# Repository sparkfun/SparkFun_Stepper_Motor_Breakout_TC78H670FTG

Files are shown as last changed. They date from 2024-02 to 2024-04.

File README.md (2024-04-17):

SparkFun Mini Stepper Motor Driver - TC78H670FTG
========================================

SparkFun Mini Stepper Motor Driver - TC78H670FTG

[*SparkFun Mini Stepper Motor Driver - TC78H670FTG (ROB-25167)*](https://sparkle.sparkfun.com/sparkle/products/25167)

The SparkFun Mini Stepper Motor Driver makes it easy to start developing with the TC78H670FTG bipolar stepper motor driver from Toshiba! With its compact size *(0.6" × 0.8")* and 0.1" pin spacing, the Mini Stepper Motor Driver is perfect for small projects or prototyping on breadboards. Use our extensive [Arduino Library](https://github.com/sparkfun/SparkFun_ProDriver_TC78H670FTG_Arduino_Library) with 10 examples, and you can quickly explore the many features of this precise and small package size motor driver IC.

With a high resolution motor control, down to 1/128th of a step, the Mini Stepper Motor Driver can be operated through traditional clock-in stepping or serial commands. Both methods are demonstrated in our Arduino Library. The serial command method is especially unique in that it allows the user to precisely control the phase, torque, current limit and mixed decay ratio of each coil immediately during stepping. Most stepper motor driver ICs require the use of an external trimpot to set the current limit, but with the Mini Stepper Motor Driver, you can precisely adjust it in software, via serial commands!

Repository Contents
-------------------

* **/Documentation** - Datasheets, additional product information
* **/Hardware** - Eagle design files (.brd, .sch)
* **/Hardware/Production** - Production panel files and gerbers (.brd)

Documentation
--------------

* **[Hookup Guide](https://learn.sparkfun.com/tutorials/1200)** - A hookup guide for the SparkFun ProDriver and Mini Stepper Motor Driver (TC78H670FTG)
* **[Arduino Library](https://github.com/sparkfun/SparkFun_ProDriver_TC78H670FTG_Arduino_Library)** - Basic Arduino Library for the SparkFun ProDriver and Mini Stepper Motor Driver (TC78H670FTG)

Product Variants
----------------
* SparkFun Mini Stepper Motor Driver - TC78H670FTG
  * [ROB-25167](https://www.sparkfun.com/products/25167)- v1.0, Initial Release
* SparkFun ProDriver - Stepper Motor Driver (TC78H670FTG)
  * [ROB-16836](https://www.sparkfun.com/products/16836)- v1.0, Initial Release

Product Versions
----------------
* [v01](https://github.com/sparkfun/SparkFun_Stepper_Motor_Breakout_TC78H670FTG/releases/tag/v10) - Initial Release

License Information
-------------------

This product is _**open source**_!

Please review the LICENSE.md file for license information.

If you have any questions or concerns on licensing, please contact technical support on our [SparkFun forums](https://forum.sparkfun.com/viewforum.php?f=152).

Distributed as-is; no warranty is given.

- Your friends at SparkFun.

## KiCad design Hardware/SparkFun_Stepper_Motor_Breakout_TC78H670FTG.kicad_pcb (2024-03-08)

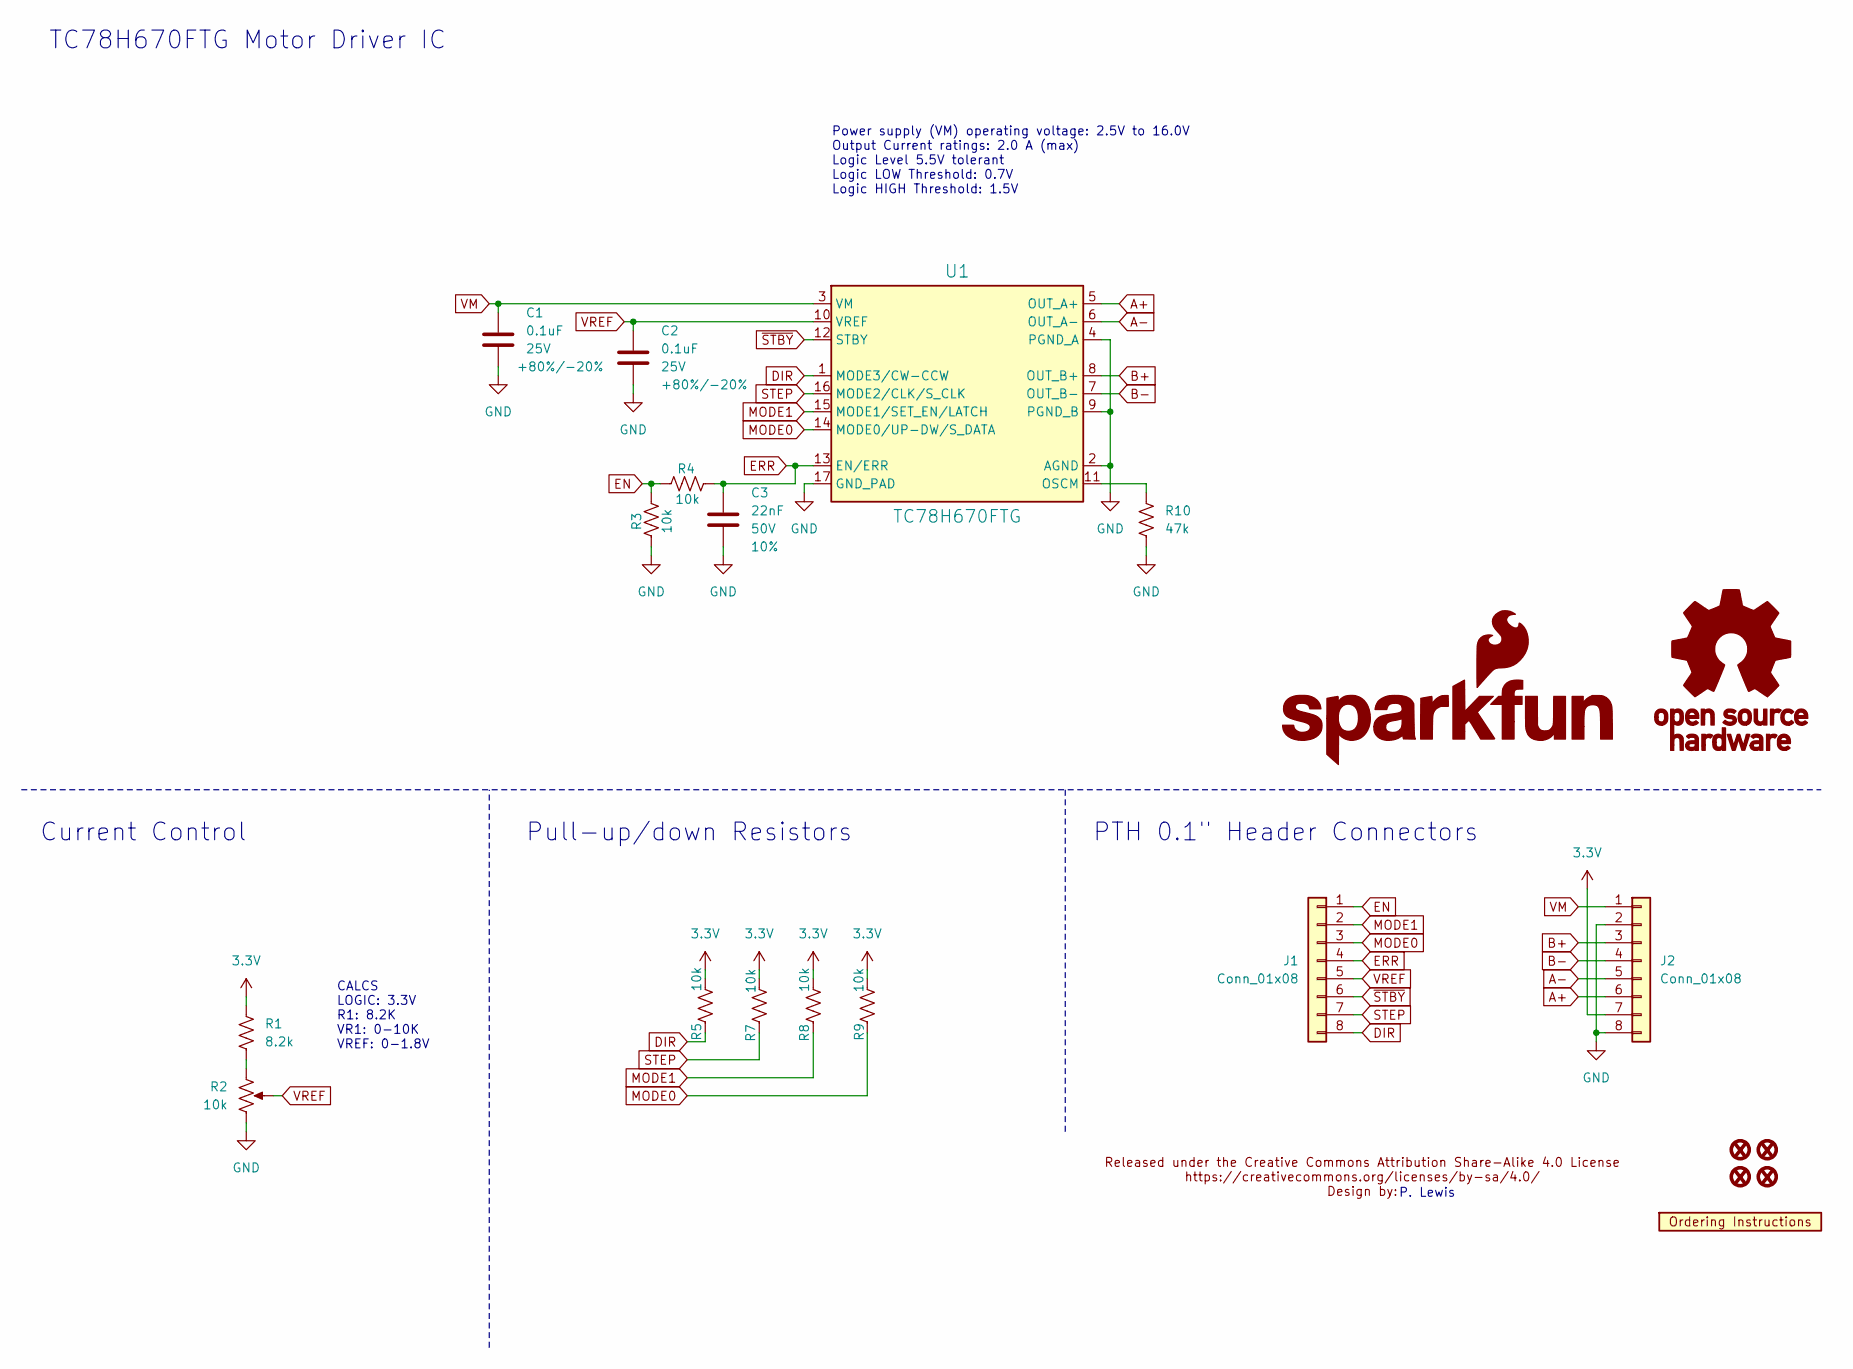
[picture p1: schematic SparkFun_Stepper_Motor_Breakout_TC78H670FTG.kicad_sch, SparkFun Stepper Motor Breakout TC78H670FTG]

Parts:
C1, C2: 0.1uF; C_0603_1608Metric; Voltage 25V; Tolerance +80%/-20%
C3: 22nF; C_0603_1608Metric; Voltage 50V; Tolerance 10%
FID1, FID2, FID3, FID4: Fiducial_0.5mm; Fiducial_0.5mm_Mask1mm
G1: SparkFun_Logo
G2: OSHW_Logo; Creative_Commons_License
J1: Conn_01x08; 1x08
J2: Conn_01x08; 1X08
R1: 8.2k; R_0603_1608Metric
R2: 10k; Trimpot_SMD_3.0x3.0mm; Mfg Part# 22AR10K
R3, R4, R5, R7, R8, R9: 10k; R_0603_1608Metric
R10: 47k; R_0603_1608Metric
U1: TC78H670FTG; P-VQFN16-0303-0.50-001
U2: Ordering_Instructions
ref**1: val**; Creative_Commons_License

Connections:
3.3V: J2.7, R1.1, R5.1, R7.1, R8.1, R9.1
A+: J2.6, U1.5 (OUT_A+)
A-: J2.5, U1.6 (OUT_A-)
B+: J2.3, U1.8 (OUT_B+)
B-: J2.4, U1.7 (OUT_B-)
DIR: J1.8, R5.2, U1.1 (MODE3/CW-CCW)
EN: J1.1, R3.1, R4.2
ERR: C3.1, J1.4, R4.1, U1.13 (EN/ERR)
GND: C1.2, C2.2, C3.2, J2.2, J2.8, R2.3, R3.2, R10.2, U1.2 (AGND), U1.4 (PGND_A), U1.9 (PGND_B), U1.17 (GND_PAD)
MODE0: J1.3, R9.2, U1.14 (MODE0/UP-DW/S_DATA)
MODE1: J1.2, R8.2, U1.15 (MODE1/SET_EN/LATCH)
unnamed: R1.2, R2.1
unnamed: R10.1, U1.11 (OSCM)
STEP: J1.7, R7.2, U1.16 (MODE2/CLK/S_CLK)
VM: C1.1, J2.1, U1.3 (VM)
VREF: C2.1, J1.5, R2.2, U1.10 (VREF)
~STBY: J1.6, U1.12 (STBY)

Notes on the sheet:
Current Control
P. Lewis
Pull-up/down Resistors
CALCS LOGIC: 3.3V R1: 8.2K VR1: 0-10K VREF: 0-1.8V
Power supply (VM) operating voltage: 2.5V to 16.0V Output Current ratings: 2.0 A (max) Logic Level 5.5V tolerant Logic LOW Threshold: 0.7V Logic HIGH Threshold: 1.5V
PTH 0.1" Header Connectors
TC78H670FTG Motor Driver IC

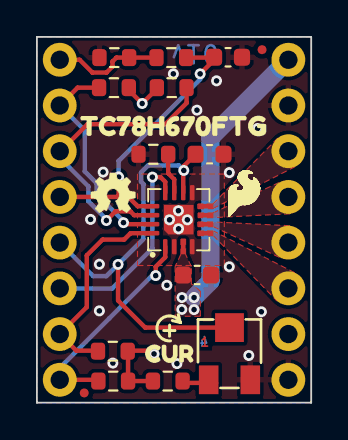
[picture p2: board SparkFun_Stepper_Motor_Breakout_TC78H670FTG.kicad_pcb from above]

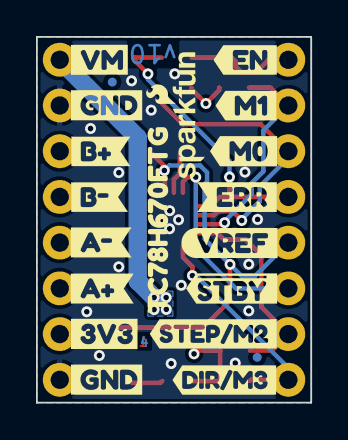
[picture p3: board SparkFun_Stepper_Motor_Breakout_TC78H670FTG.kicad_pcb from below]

Board: 4 copper layers, 15.2 x 20.3 mm, 42 parts (19 on the bottom side), 17 nets.

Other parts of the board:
Ref**: Val**; OSHW_Logo_2.5mm
kibuzzard-65CFAA22: G***; kibuzzard-65CFAA22
kibuzzard-65CFAA33, kibuzzard-65CFAA33#2: G***; kibuzzard-65CFAA33
kibuzzard-65CFAAF8: G***; kibuzzard-65CFAAF8
kibuzzard-65CFAB5A: G***; kibuzzard-65CFAB5A
kibuzzard-65CFAB77: G***; kibuzzard-65CFAB77
kibuzzard-65CFAB85: G***; kibuzzard-65CFAB85
kibuzzard-65CFAC2F: G***; kibuzzard-65CFAC2F
kibuzzard-65CFAC5D: G***; kibuzzard-65CFAC5D
kibuzzard-65CFAC9C: G***; kibuzzard-65CFAC9C
kibuzzard-65CFAC13: G***; kibuzzard-65CFAC13
kibuzzard-65CFAC42: G***; kibuzzard-65CFAC42
kibuzzard-65CFAD2C: G***; kibuzzard-65CFAD2C
kibuzzard-65CFAE3D: G***; kibuzzard-65CFAE3D
kibuzzard-65CFAE6E, kibuzzard-65CFAE6E#2: G***; kibuzzard-65CFAE6E
kibuzzard-65D52B03: G***; kibuzzard-65D52B03
kibuzzard-65D52B32: G***; kibuzzard-65D52B32
kibuzzard-65D531EE: G***; kibuzzard-65D531EE

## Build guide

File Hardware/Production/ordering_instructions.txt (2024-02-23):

Ordering Instructions:
Panel dimensions: 107.64 x 117.30 mm.
Material: TG135-140
Solder Mask: Red
Silkscreen: White
Layers: 4
Finish: HASL Lead Free
Thickness: 1.6mm
2.0oz Outer Layers
0.5oz Inner Layers
Minimum track width: 0.25mm (9.84mil)
Minimum via drill: 0.30mm (12.00mil)

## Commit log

2024-02-16 initial layout
    [SparkFun_Stepper_Motor_Carrier_TC78H670FTG.kicad_pcb, SparkFun_Stepper_Motor_Carrier_TC78H670FTG.kicad_sch]
2024-02-16 version in bottom copper
    [SparkFun_Stepper_Motor_Carrier_TC78H670FTG.kicad_pcb]
2024-02-19 spoke angle fix on trimpot footprint
    [SparkFun_Stepper_Motor_Carrier_TC78H670FTG.kicad_pcb]
2024-02-19 removed project directory
    -all files are now directly in "hardware" folder
    [SparkFun_Stepper_Motor_Carrier_TC78H670FTG.kicad_pcb, SparkFun_Stepper_Motor_Carrier_TC78H670FTG.kicad_sch]
2024-02-19 review notes round 1
    -SCH
    --general cleanup
    --fiducials
    --section lines
    --SFE logo
    --OSHW logo
    --voltage and current rating
    --showing U1 reference and value
    -BOARD
    --flipped version number on board
    --designer name
    --ordering instructions
    --CC license
    --SFE logo
    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
    [SparkFun_Stepper_Motor_Carrier_TC78H670FTG.kicad_pcb, SparkFun_Stepper_Motor_Carrier_TC78H670FTG.kicad_sch]
2024-02-20 sch max voltage note
    -and more gitignore
    [SparkFun_Stepper_Motor_Carrier_TC78H670FTG.kicad_sch]
2024-02-20 schematic cleanup
    -section titles
    [SparkFun_Stepper_Motor_Carrier_TC78H670FTG.kicad_sch]
2024-02-20 more stuff pre-review
    -copper weight added to ordering instructions
    -removed old sym library from project table (eagle import from older prodriver)
    -added CC license to sch
    -added M2 and M3 to buzzard labels for STEP and DIR
    -copper edge clearance in DRC set to 0.2mm
    -excluded DRC errors that I wish to ignore
    -used one signle GND zone for top in1 and bottom copper ground pours
    -adjusted clearances/min-widths/spoke-thickness/DRC to get ideal GND zone flow.
    [SparkFun_Stepper_Motor_Carrier_TC78H670FTG.kicad_pcb, SparkFun_Stepper_Motor_Carrier_TC78H670FTG.kicad_sch]
2024-02-21 add sfe flame logo
    [SparkFun_Stepper_Motor_Carrier_TC78H670FTG.kicad_pcb]
2024-02-21 changing file names to "breakout"
    [SparkFun_Stepper_Motor_Breakout_TC78H670FTG.kicad_pcb, SparkFun_Stepper_Motor_Breakout_TC78H670FTG.kicad_sch]
2024-02-21 more tweaks for DRC
    -inner layer zone properties min width changed from .3 to .2 to allow flow and more thermal spokes on 3v3 header
    -DRC exclusions for fiducials
    [SparkFun_Stepper_Motor_Breakout_TC78H670FTG.kicad_pcb]
2024-02-21 ordering instructions
    Inner copper weight
    Material: TG135
    Four layer stack-up
    [SparkFun_Stepper_Motor_Breakout_TC78H670FTG.kicad_pcb]
2024-02-21 layout tweaks
    -added gnd via near serial data line transition
    -reduced via sized to 12mil to avoid drc errors and make room
    [SparkFun_Stepper_Motor_Breakout_TC78H670FTG.kicad_pcb]
2024-02-21 moved fiducials inward
    [SparkFun_Stepper_Motor_Breakout_TC78H670FTG.kicad_pcb]
2024-02-22 updated trimpot
    [SparkFun_Stepper_Motor_Breakout_TC78H670FTG.kicad_pcb, SparkFun_Stepper_Motor_Breakout_TC78H670FTG.kicad_sch]
2024-02-22 corrected motor driver IC footprint
    I had the pins numbered incorrectly, had to re-route most things.
    [SparkFun_Stepper_Motor_Breakout_TC78H670FTG.kicad_pcb, SparkFun_Stepper_Motor_Breakout_TC78H670FTG.kicad_sch]
2024-02-22 checklist stuff
    -added 1,2,3,4 to copper layers
    [SparkFun_Stepper_Motor_Breakout_TC78H670FTG.kicad_pcb]
2024-02-23 nudged VM - bottom gnd flow
    [SparkFun_Stepper_Motor_Breakout_TC78H670FTG.kicad_pcb]
2024-02-23 reduced paste on driver IC
    [SparkFun_Stepper_Motor_Breakout_TC78H670FTG.kicad_pcb]
2024-02-23 step routed directly away from ic
    [SparkFun_Stepper_Motor_Breakout_TC78H670FTG.kicad_pcb]
2024-02-23 more gnd vias
    [SparkFun_Stepper_Motor_Breakout_TC78H670FTG.kicad_pcb]
2024-02-23 version to v10
    [SparkFun_Stepper_Motor_Breakout_TC78H670FTG.kicad_pcb]
2024-02-23 production panel and gerbers v10c
    [SparkFun_Stepper_Motor_Breakout_TC78H670FTG_panelized.GBL, SparkFun_Stepper_Motor_Breakout_TC78H670FTG_panelized.GBO, SparkFun_Stepper_Motor_Breakout_TC78H670F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]
2024-02-28 library work and sch cleanup
    -moved to a 0.05" grid for schematic and tightened things up (made all nets shorter to match smaller grid and only use a single grid space to extend out from any pin)
    -updated ordering instructions fp to avoid sch->brd update error
    [SparkFun_Stepper_Motor_Breakout_TC78H670FTG.kicad_pcb, SparkFun_Stepper_Motor_Breakout_TC78H670FTG.kicad_sch]
2024-03-08 removing duplicate trimpot in PCB file
    [SparkFun_Stepper_Motor_Breakout_TC78H670FTG.kicad_pcb]
2024-04-17 Create LICENSE.md
    Remove carriage returns
    Fix grammar

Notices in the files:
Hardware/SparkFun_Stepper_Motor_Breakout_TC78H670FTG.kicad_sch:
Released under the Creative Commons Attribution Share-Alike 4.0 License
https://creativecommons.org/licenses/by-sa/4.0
